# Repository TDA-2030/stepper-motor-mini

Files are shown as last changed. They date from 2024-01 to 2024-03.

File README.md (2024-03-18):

# Stepper Motor mini

A very simple and low-cost  stepper motor controller based on [dummy robot](https://gitee.com/switchpi/dummy)

## How to build

build on Windows

1. Download toolchain from https://github.com/xpack-dev-tools/arm-none-eabi-gcc-xpack/releases and unzip it.
2. run follow command to build
    ```shell
    mkdir build
    cmake -G "MinGW Makefiles" ..
    ```

## Feature

- Power: 12v~24v
- 2-layer board
- mini size
- Modbus support

## Preview

<center>
<figure>
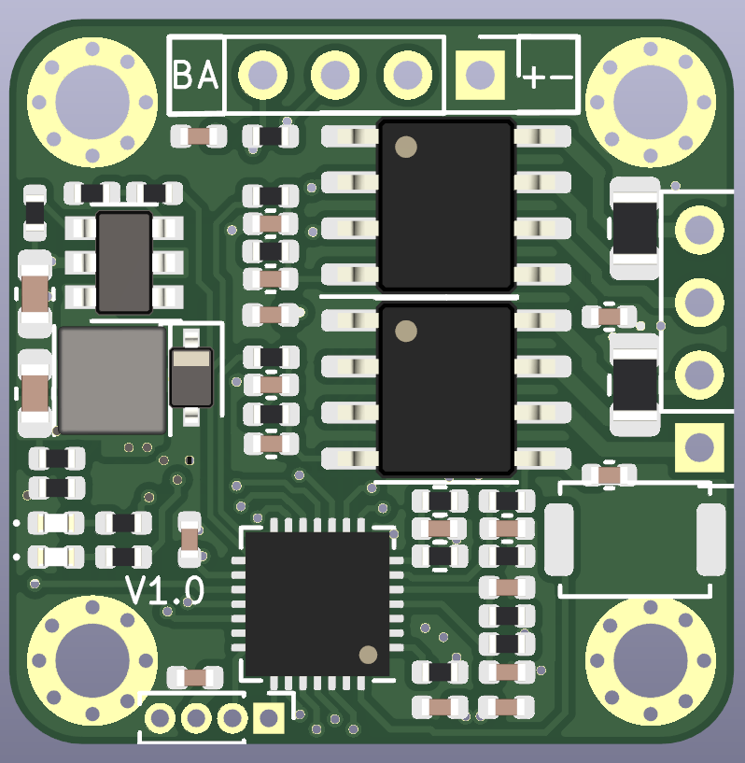
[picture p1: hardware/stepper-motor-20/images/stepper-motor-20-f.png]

·
·
·
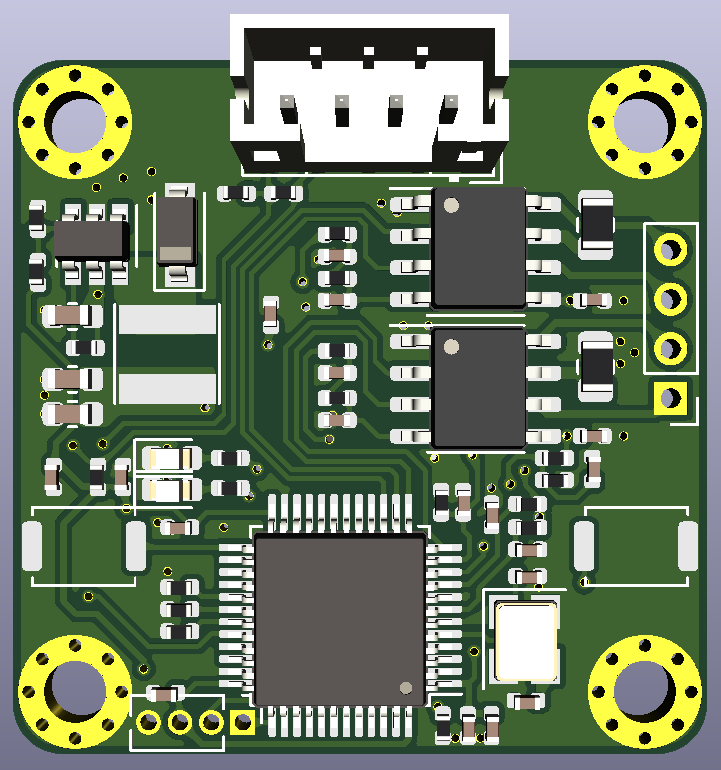
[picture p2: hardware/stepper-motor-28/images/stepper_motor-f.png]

</figure>
</center>

## Uasge

### Button Functions

| Action | Function |
| --- | --- |
| click | toggle to run or stop |
| long press | restore settings |

### calibration

push down the button then power on, the motor well start to calibration sensor.

### Modbus Register

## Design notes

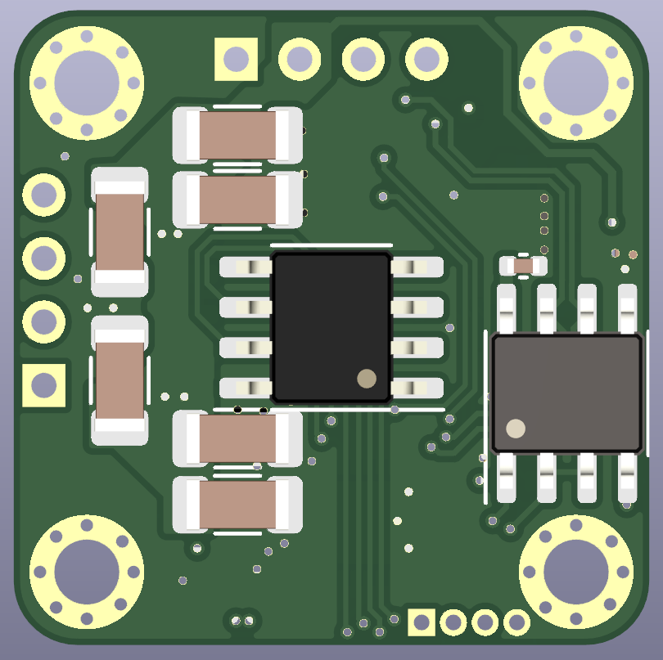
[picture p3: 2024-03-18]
hardware/stepper-motor-20/images/stepper-motor-20-b.png

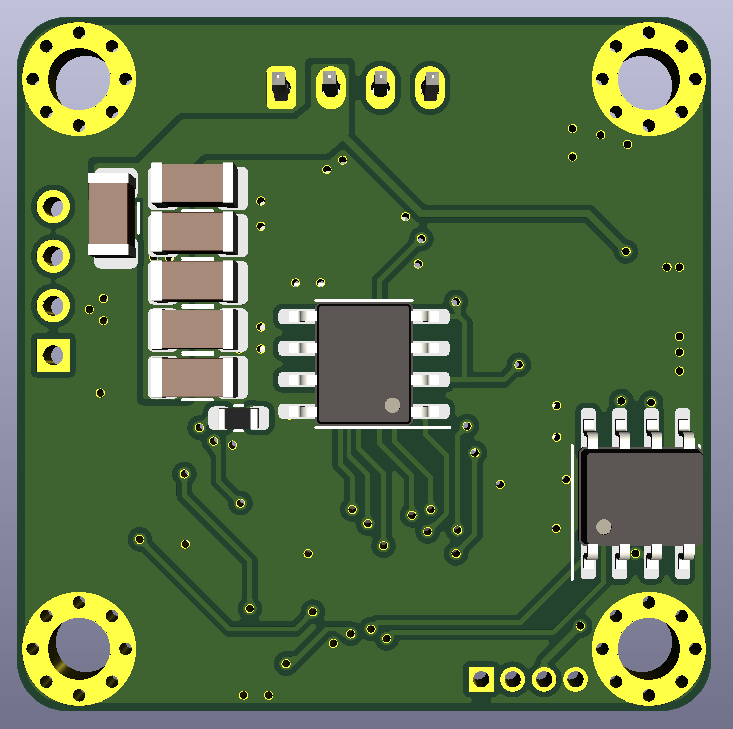
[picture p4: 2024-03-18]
hardware/stepper-motor-28/images/stepper_motor-b.png

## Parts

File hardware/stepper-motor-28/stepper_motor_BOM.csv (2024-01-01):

Comment | Description | Designator | Footprint | LibRef | Pins | Quantity | PartNumber | url
15p | desc | C1,C2, | C_0402_1005Metric | libref | 2 | 2
100n | desc | C3,C8,C11,C12,C15,C16,C19,C20,C28,C29, | C_0402_1005Metric | libref | 2 | 10
2.2u | desc | C4,C5,C6,C7,C9,C10,C24, | C_0402_1005Metric | libref | 2 | 7
10uf | desc | C25,C26,C27, | C_0603_1608Metric | libref | 2 | 3
GREEN | desc | D1, | LED_0603_1608Metric | libref | 2 | 1
RED | desc | D2, | LED_0603_1608Metric | libref | 2 | 1
B5819W SL | desc | D3, | D_SOD-123 | libref | 2 | 1
22uH | desc | L1, | L_Taiyo-Yuden_NR-40xx | libref | 2 | 1
1k | desc | R1,R2,R6,R7,R8,R9,R17, | R_0402_1005Metric | libref | 2 | 7
10k | desc | R3,R4,R16, | R_0402_1005Metric | libref | 2 | 3
0Ω | desc | R5,R21,R22,R23, | R_0402_1005Metric | libref | 2 | 4
0.1Ω | desc | R10,R11, | R_0805_2012Metric | libref | 2 | 2
3.3k | desc | R12, | R_0402_1005Metric | libref | 2 | 1
200k | desc | R13, | R_0402_1005Metric | libref | 2 | 1
33k | desc | R14, | R_0402_1005Metric | libref | 2 | 1
100k | desc | R15, | R_0402_1005Metric | libref | 2 | 1
120R | desc | R18, | R_0402_1005Metric | libref | 2 | 1
360R | desc | R19,R20, | R_0402_1005Metric | libref | 2 | 2
STM32F103CBTx | desc | U2, | LQFP-48_7x7mm_P0.5mm | libref | 48 | 1
TB67H450FNG | desc | U3,U4, | SOIC-8-1EP_3.9x4.9mm_P1.27mm_EP2.41x3.3mm | libref | 13 | 2
TX4137 | desc | U5, | SOT-23-6 | libref | 6 | 1
8MHz | desc | Y1, | Crystal_SMD_3225-4Pin_3.2x2.5mm | libref | 4 | 1
SW_Push | desc | SW2,SW3, | SW_Push_SPST_NO_Alps_SKRK | libref | 2 | 2
22uF, 25V | desc | C13,C14,C17,C18,C21,C22, | C_1206_3216Metric | libref | 2 | 6
MT6816 | desc | U1, | SOIC-8_3.9x4.9mm_P1.27mm | libref | 8 | 1
SP3485EP | desc | U6, | SOIC-8_3.9x4.9mm_P1.27mm | libref | 8 | 1
NTC 10k | desc | NTC1, | R_0603_1608Metric | libref | 2 | 1
Through Hole Items
MountingHole_Pad | desc | H1,H2,H3,H4, | MountingHole_2.5mm_Pad_Via | libref | 9 | 4
CON | desc | J1, | JST_PH_B4B-PH-K_1x04_P2.00mm_Vertical | libref | 4 | 1
SWD | desc | J2, | PinHeader_1x04_P1.27mm_Vertical | libref | 4 | 1
MOTOR | desc | J3, | PinHeader_1x04_P2.00mm_Vertical | libref | 4 | 1

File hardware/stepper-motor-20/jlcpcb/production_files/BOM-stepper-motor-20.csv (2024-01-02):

Comment | Designator | Footprint | LCSC
100n | C3 | C_0402_1005Metric
2.2u | C4 | C_0402_1005Metric
2.2u | C5 | C_0402_1005Metric
2.2u | C6 | C_0402_1005Metric
2.2u | C7 | C_0402_1005Metric
100n | C8 | C_0402_1005Metric
2.2u | C9 | C_0402_1005Metric
2.2u | C10 | C_0402_1005Metric
100n | C12 | C_0402_1005Metric
100n | C16 | C_0402_1005Metric
100n | C19 | C_0402_1005Metric
100n | C20 | C_0402_1005Metric
10uf | C24 | C_0603_1608Metric
100n | C26 | C_0402_1005Metric
GREEN | D1 | LED_0402_1005Metric
RED | D2 | LED_0402_1005Metric
1N5819 | D3 | D_SOD-323
MountingHole_Pad | H1 | MountingHole_2.0mm_Pad_Via
MountingHole_Pad | H2 | MountingHole_2.0mm_Pad_Via
MountingHole_Pad | H3 | MountingHole_2.0mm_Pad_Via
SWD | J2 | PinHeader_1x04_P1.00mm_Vertical
MOTOR | J3 | PinHeader_1x04_P2.00mm_Vertical
22uH | L1 | L_Taiyo-Yuden_MD-3030
1k | R2 | R_0402_1005Metric
10k | R3 | R_0402_1005Metric
10k | R4 | R_0402_1005Metric
0Ω | R5 | R_0402_1005Metric
1k | R7 | R_0402_1005Metric
1k | R9 | R_0402_1005Metric
0.1Ω | R10 | R_0805_2012Metric
0.1Ω | R11 | R_0805_2012Metric
200k | R12 | R_0402_1005Metric
33k | R13 | R_0402_1005Metric
100k | R14 | R_0402_1005Metric
10k | R15 | R_0402_1005Metric
120R | R18 | R_0402_1005Metric
4.7k | R19 | R_0402_1005Metric
GD32F150G8U6TR | U2 | QFN-28-1EP_4x4mm_P0.4mm_EP2.6x2.6mm
TB67H450FNG | U3 | SOIC-8-1EP_3.9x4.9mm_P1.27mm_EP2.41x3.3mm
TB67H450FNG | U4 | SOIC-8-1EP_3.9x4.9mm_P1.27mm_EP2.41x3.3mm
TX4137 | U5 | SOT-23-6
MountingHole_Pad | H4 | MountingHole_2.0mm_Pad_Via
1k | R16 | R_0402_1005Metric
3.3k | R17 | R_0402_1005Metric
1k | R1 | R_0402_1005Metric
4.7k | R20 | R_0402_1005Metric
1k | R6 | R_0402_1005Metric
CON | J1 | PinHeader_1x04_P2.00mm_Vertical
1k | R8 | R_0402_1005Metric
100n | C15 | C_0402_1005Metric
100n | C11 | C_0402_1005Metric
SW_Push | SW1 | SW_Push_SPST_NO_Alps_SKRK
2.2u | C27 | C_0402_1005Metric
NTC 10k | NTC1 | R_0402_1005Metric
10uf | C23 | C_0603_1608Metric
22uF, 25V | C13 | C_1206_3216Metric
22uF, 25V | C14 | C_1206_3216Metric
22uF, 25V | C17 | C_1206_3216Metric
22uF, 25V | C18 | C_1206_3216Metric
22uF, 25V | C21 | C_1206_3216Metric
22uF, 25V | C22 | C_1206_3216Metric
MT6816 | U1 | SOP-8_3.76x4.96mm_P1.27mm
SP3485EP | U6 | SOIC-8_3.9x4.9mm_P1.27mm
100n | C28 | C_0402_1005Metric

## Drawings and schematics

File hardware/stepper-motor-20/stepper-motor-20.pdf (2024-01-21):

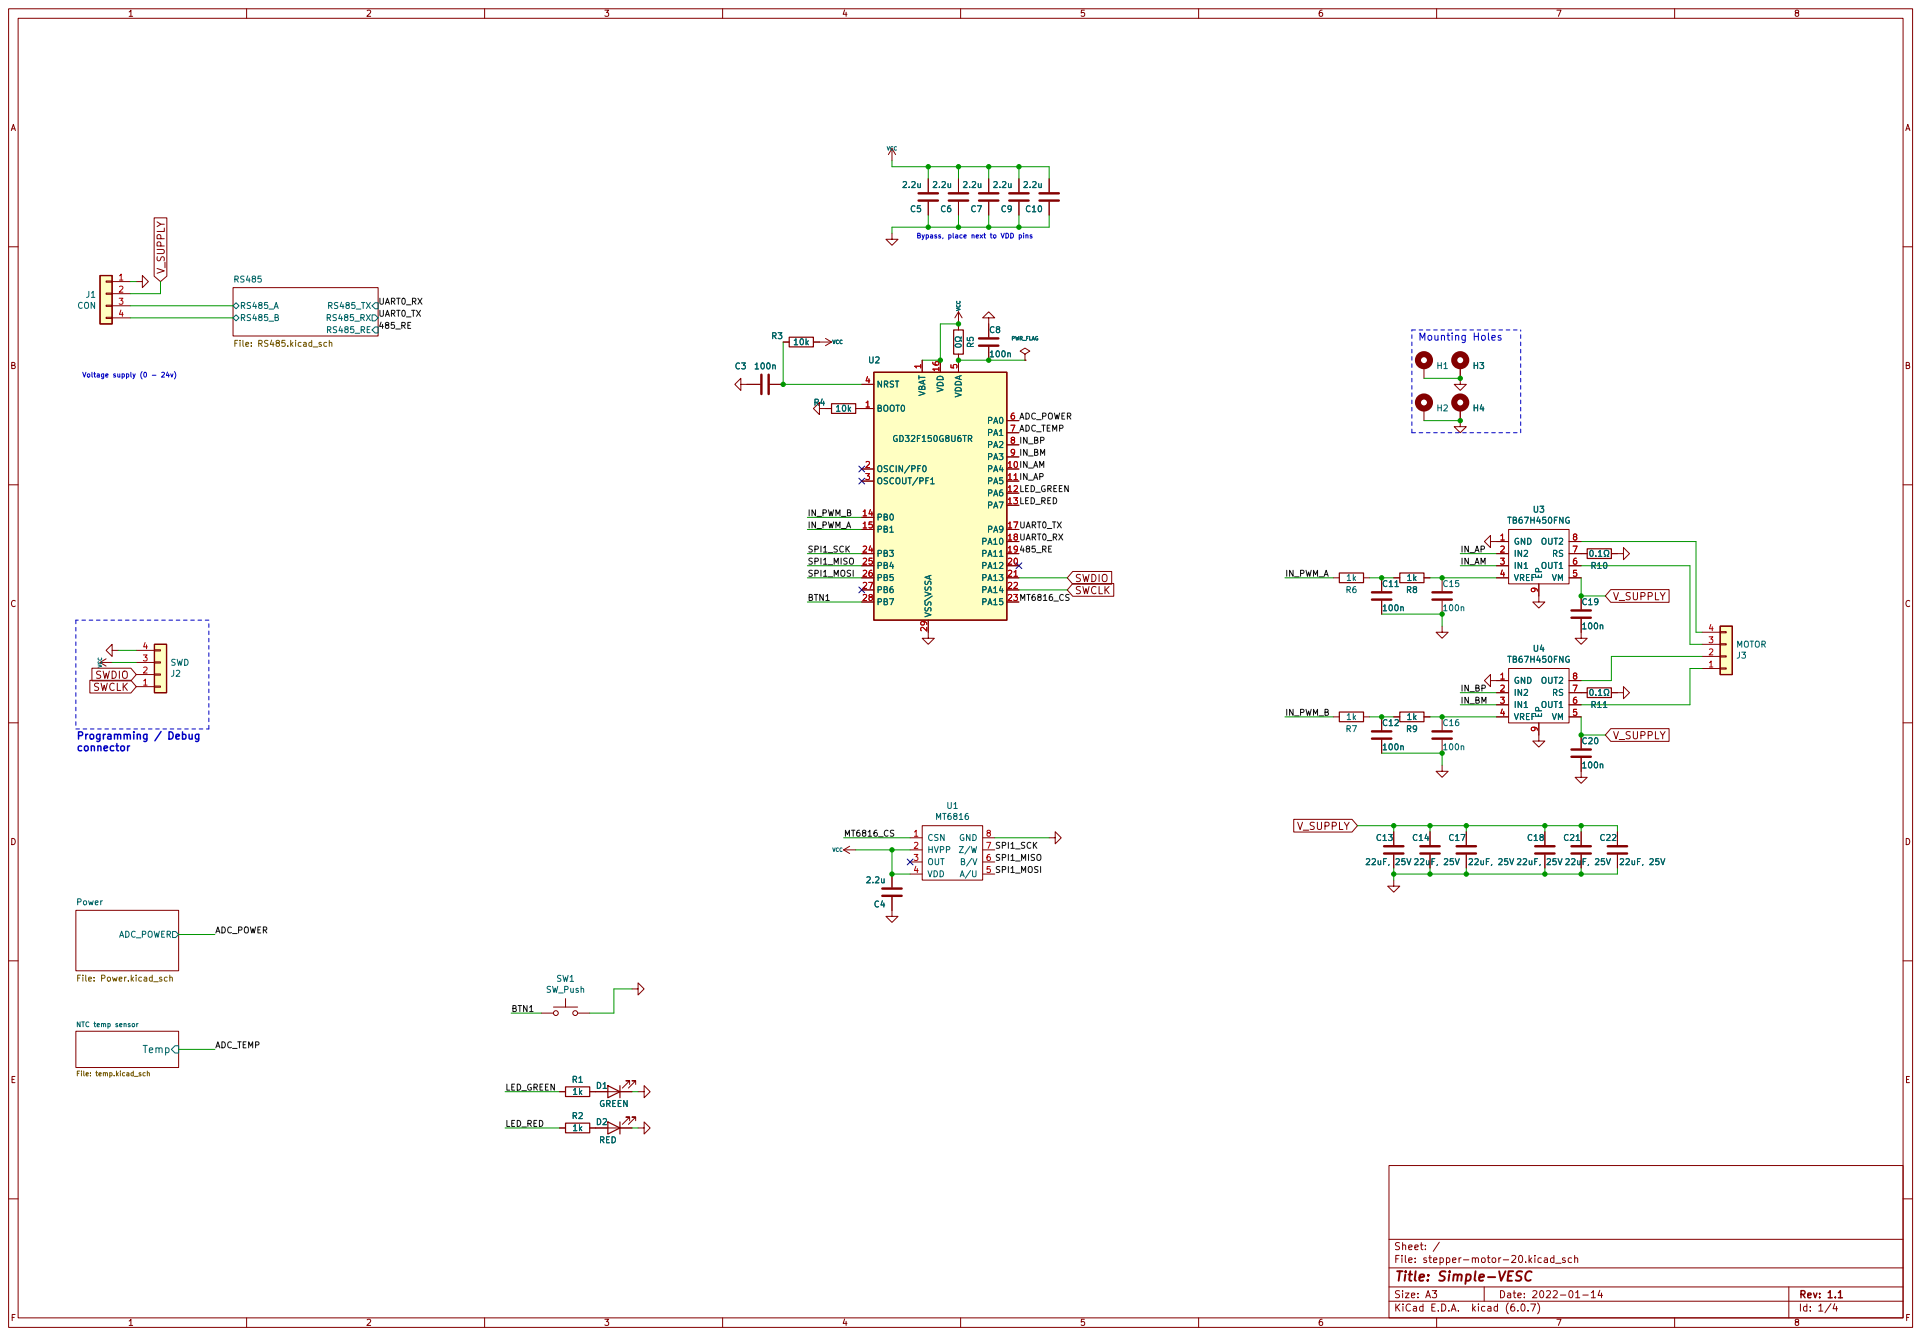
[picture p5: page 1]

V_SUPPLY
Voltage supply (0 - 24v) Programming / Debug

Bypass, place next to VDD pins

1 PA4 10 PA5 11 PA6 12 PA7 13 PB0 14 PB1 15 VDD 16 PA9 17 PA10 18 PA11 19 OSCIN/PF0 2 PA12 20 PA13 21 PA14 22 PA15 23 PB3 24 PB4 25 PB5 26 PB6 27 PB7 28 VSS\VSSA 29 OSCOUT/PF1 3 NRST 4 VDDA

NTC temp sensor File: temp.kicad_sch ADC_POWER

File: stepper-motor-20.kicad_sch Sheet: / Temp

Id: 1/4 Title: Simple-VESC

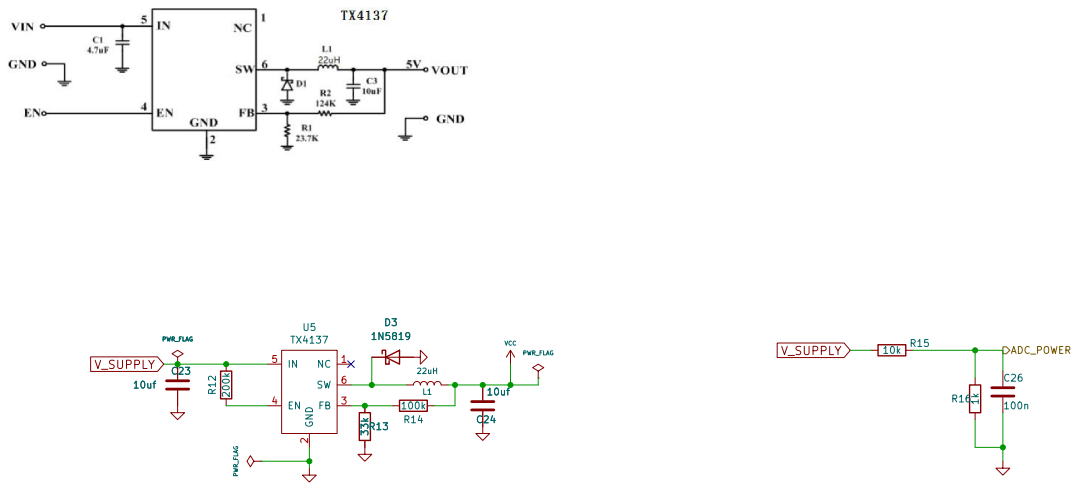
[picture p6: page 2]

File: Power.kicad_sch Sheet: /Power/ R13 33k

Id: 2/4 Title: Simple-VESC

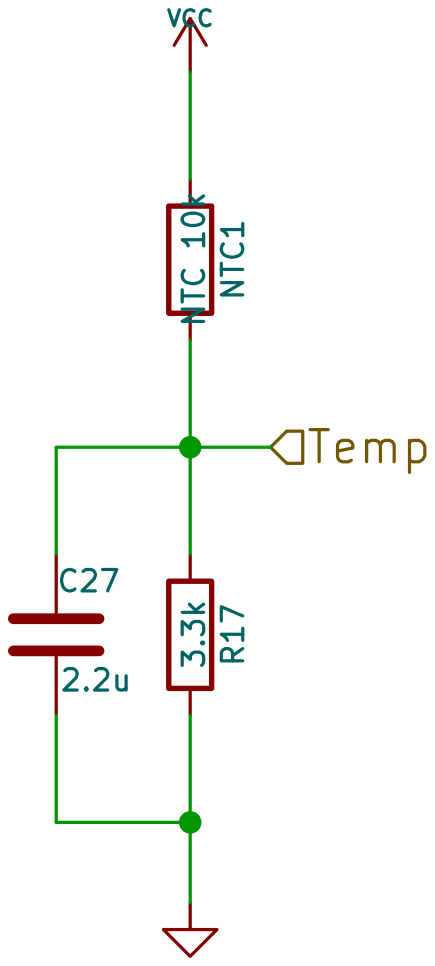
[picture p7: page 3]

Sheet: /NTC temp sensor/ 3.3k R17 C27

File: temp.kicad_sch
Id: 3/4 Title: Simple-VESC

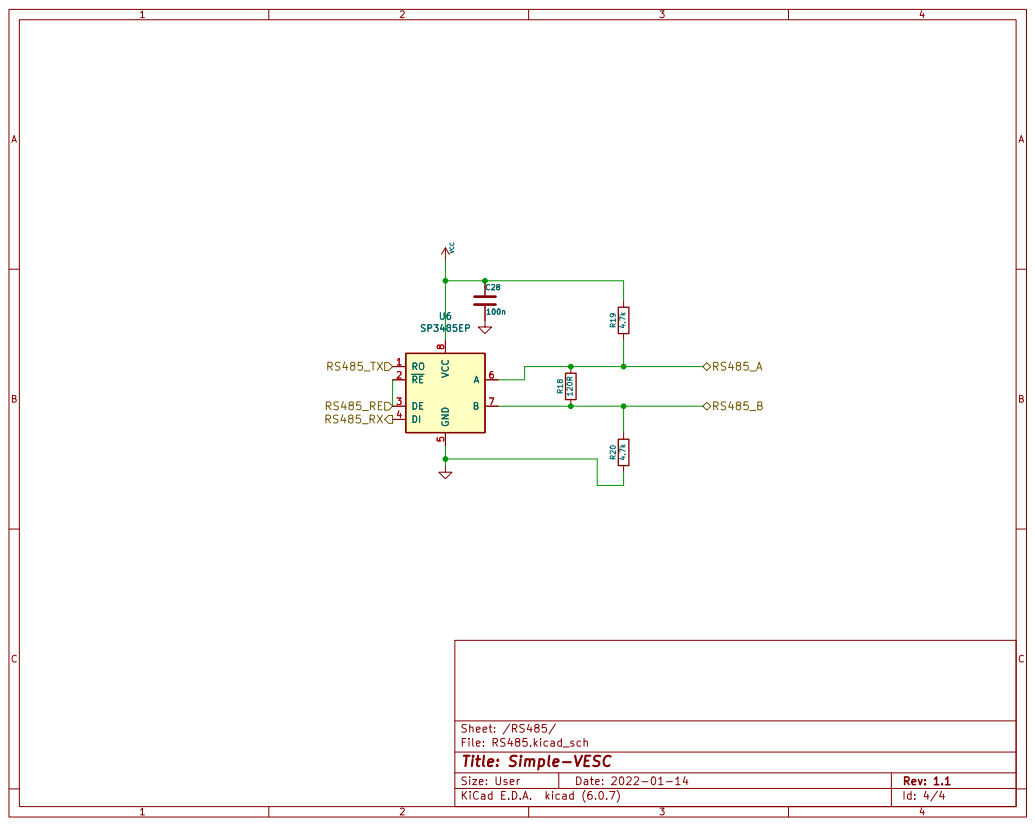
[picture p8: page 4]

Id: 4/4 Title: Simple-VESC

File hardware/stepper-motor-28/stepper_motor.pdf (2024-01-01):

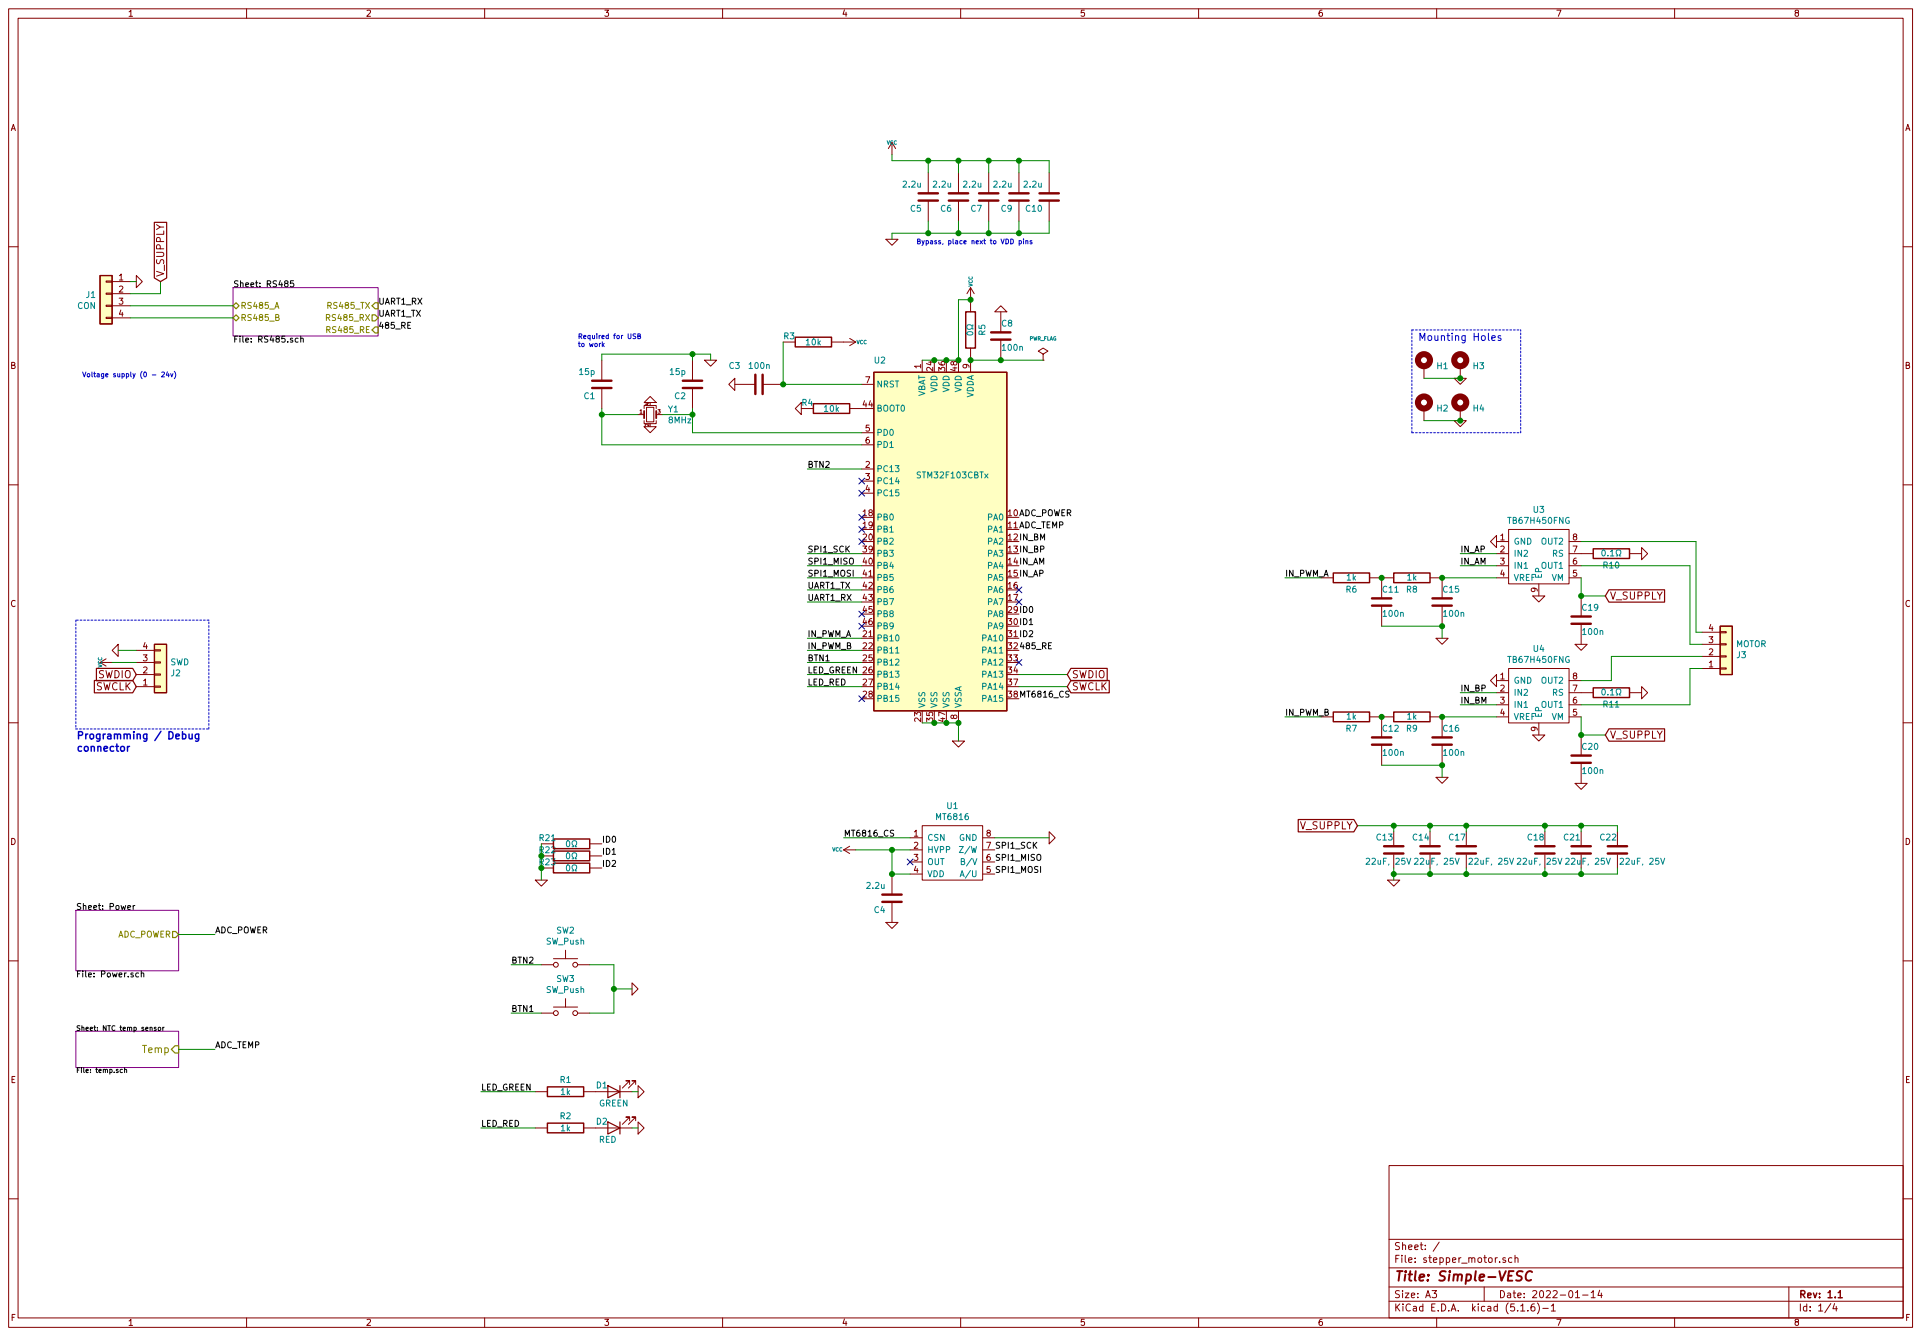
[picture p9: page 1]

Bypass, place next to VDD pins Required for USB

to work Programming / Debug

1 VDD 24 VDD 36 VDD 48 VDDA

9 VSS 23 VSS 35 VSS 47 VSSA

Sheet: Power File: Power.sch ADC_POWER

Id: 1/4 Title: Simple-VESC

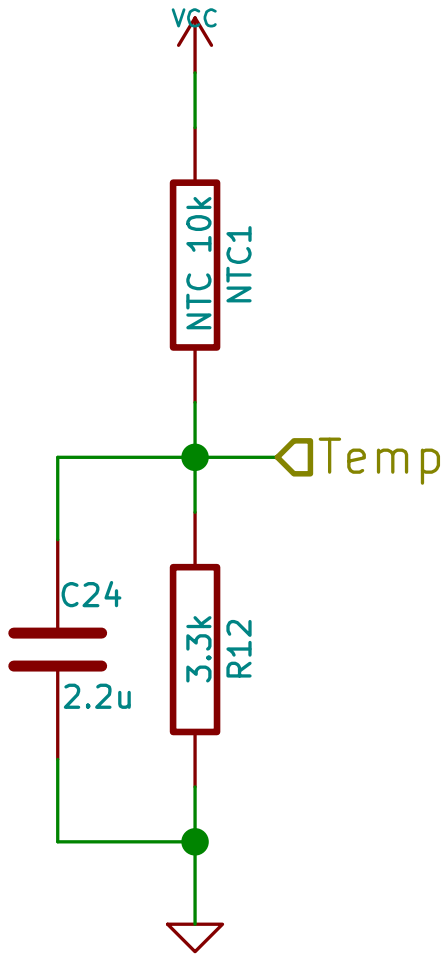
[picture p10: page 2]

Sheet: /NTC temp sensor/ 3.3k R12 C24

File: temp.sch
Id: 2/4 Title: Simple-VESC

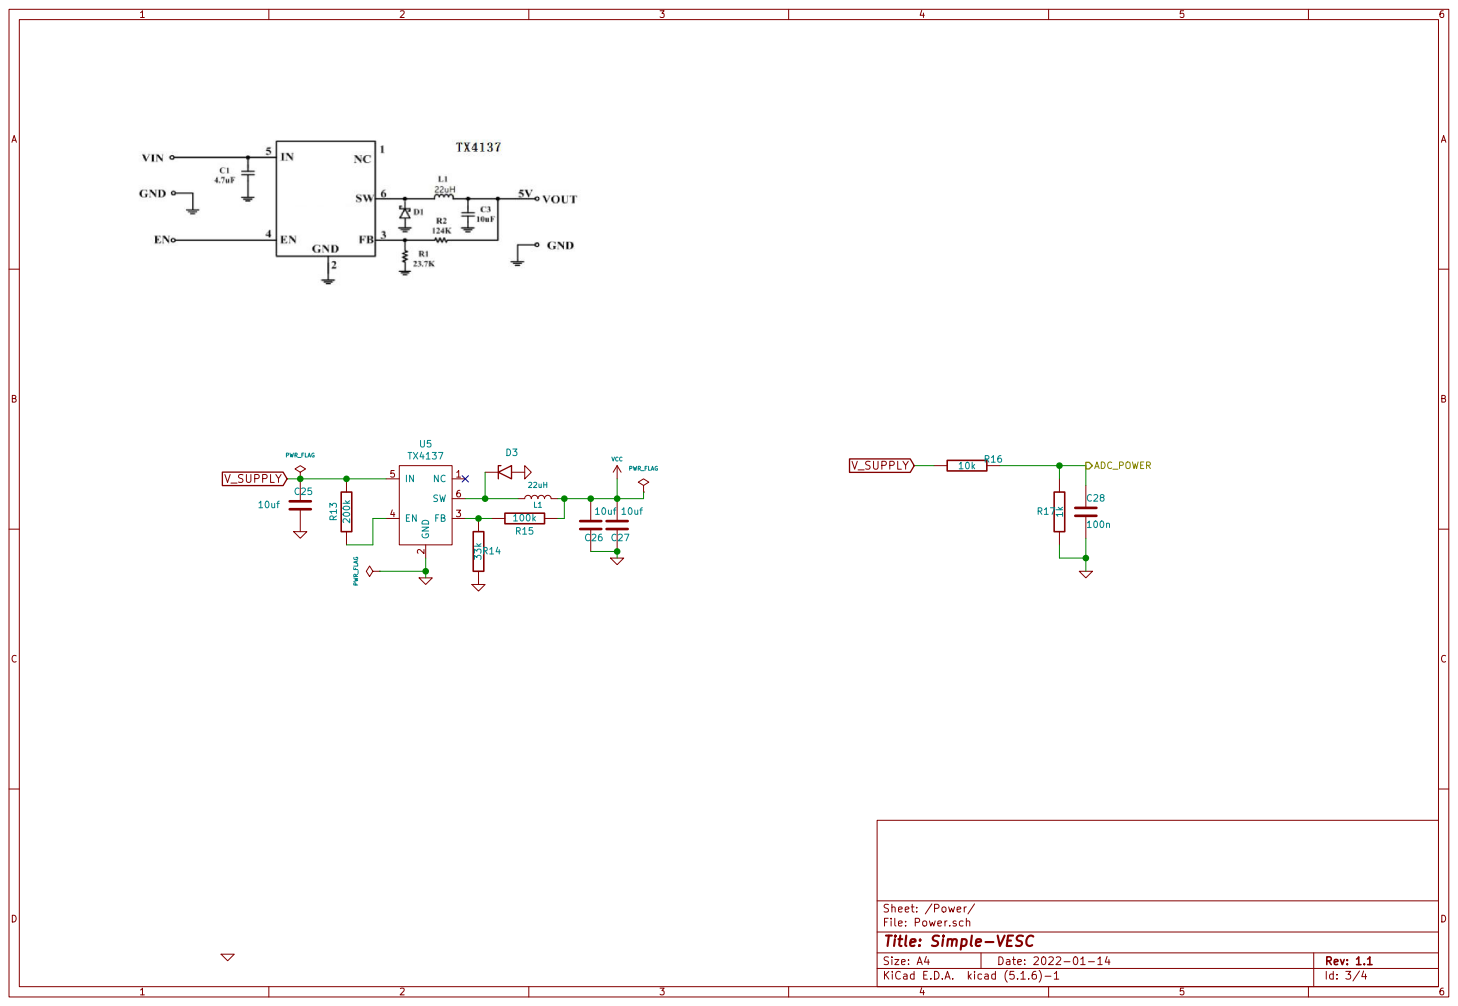
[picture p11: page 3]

File: Power.sch Sheet: /Power/ C26

Id: 3/4 Title: Simple-VESC

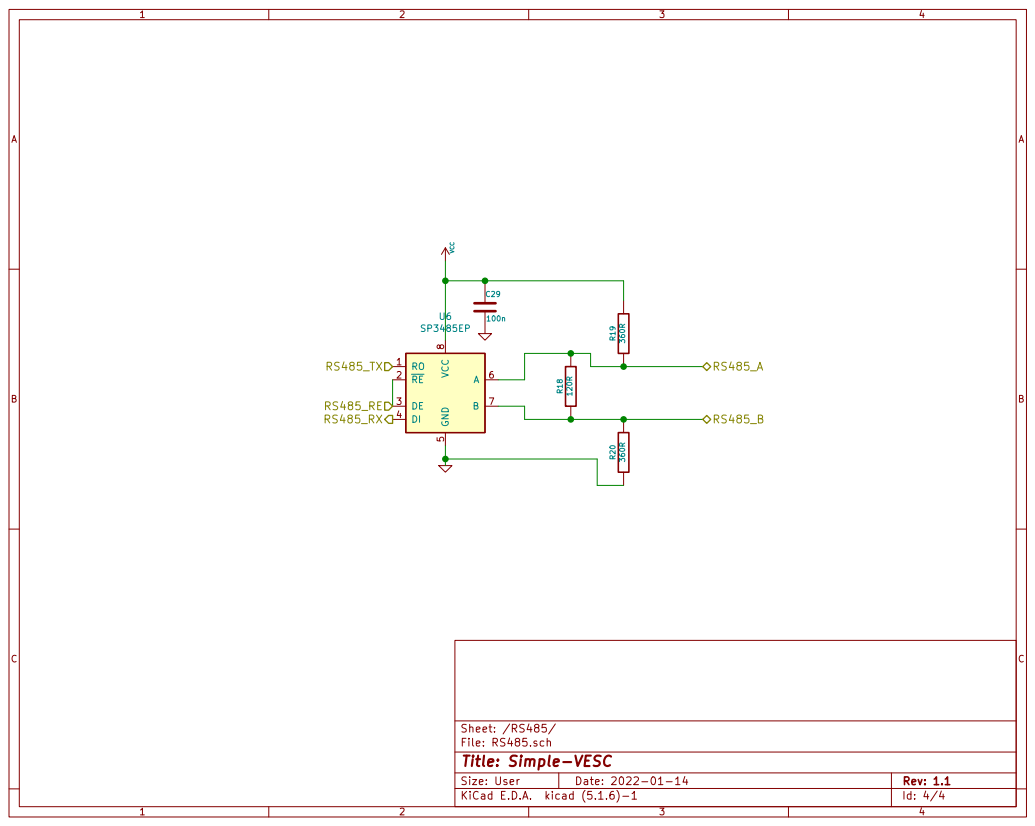
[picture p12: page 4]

Id: 4/4 Title: Simple-VESC

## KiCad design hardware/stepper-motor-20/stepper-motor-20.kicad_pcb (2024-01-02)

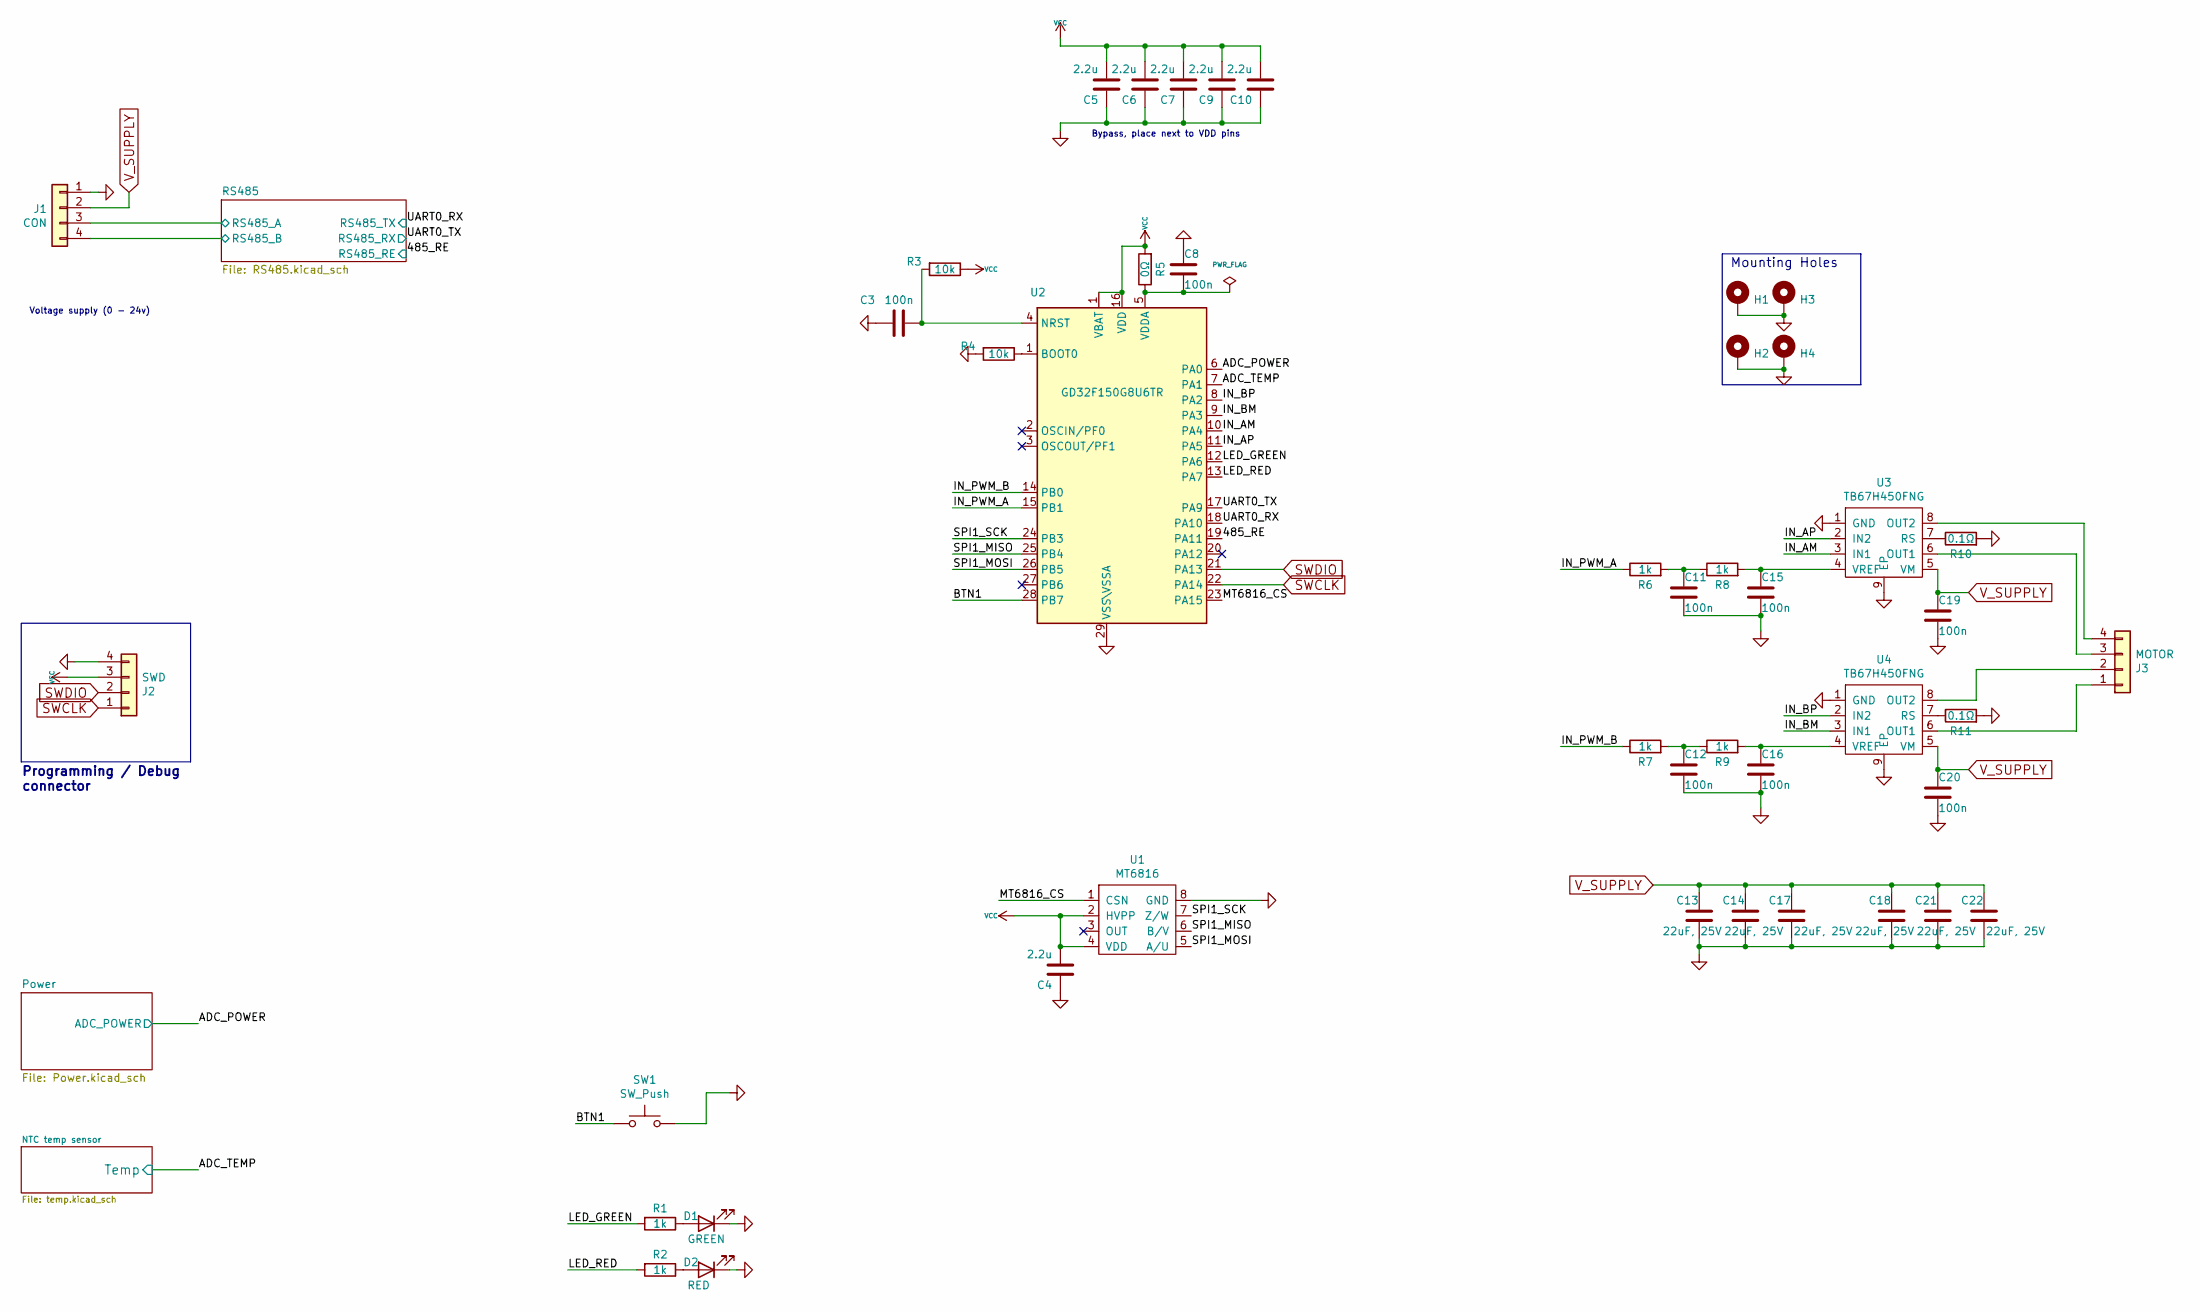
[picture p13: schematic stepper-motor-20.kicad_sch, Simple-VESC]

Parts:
C3, C8, C11, C12, C15, C16, C19, C20: 100n; C_0402_1005Metric
C4, C5, C6, C7, C9, C10: 2.2u; C_0402_1005Metric
C13, C14, C17, C18, C21, C22: 22uF, 25V; C_1206_3216Metric
D1: GREEN; LED_0402_1005Metric
D2: RED; LED_0402_1005Metric
H1, H2, H3, H4: MountingHole_Pad; MountingHole_2.0mm_Pad_Via
J1: CON; PinHeader_1x04_P2.00mm_Vertical
J2: SWD; PinHeader_1x04_P1.00mm_Vertical
J3: MOTOR; PinHeader_1x04_P2.00mm_Vertical
R1, R2, R6, R7, R8, R9: 1k; R_0402_1005Metric
R3, R4: 10k; R_0402_1005Metric
R5: 0Ω; R_0402_1005Metric
R10, R11: 0.1Ω; R_0805_2012Metric
SW1: SW_Push; SW_Push_SPST_NO_Alps_SKRK
U1: MT6816; SOP-8_3.76x4.96mm_P1.27mm
U2: GD32F150G8U6TR; QFN-28-1EP_4x4mm_P0.4mm_EP2.6x2.6mm
U3, U4: TB67H450FNG; SOIC-8-1EP_3.9x4.9mm_P1.27mm_EP2.41x3.3mm

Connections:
/485_RE: U2.19 (PA11); also elsewhere on the board
/ADC_POWER: U2.6 (PA0); also elsewhere on the board
/ADC_TEMP: U2.7 (PA1); also elsewhere on the board
/BTN1: SW1.1, U2.28 (PB7)
/IN_AM: U2.10 (PA4), U3.3 (IN1)
/IN_AP: U2.11 (PA5), U3.2 (IN2)
/IN_BM: U2.9 (PA3), U4.3 (IN1)
/IN_BP: U2.8 (PA2), U4.2 (IN2)
/IN_PWM_A: R6.1, U2.15 (PB1)
/IN_PWM_B: R7.1, U2.14 (PB0)
/LED_GREEN: R1.2, U2.12 (PA6)
/LED_RED: R2.2, U2.13 (PA7)
/MT6816_CS: U1.1 (CSN), U2.23 (PA15)
/RS485/RS485_A: J1.3; also elsewhere on the board
/RS485/RS485_B: J1.4; also elsewhere on the board
/SPI1_MISO: U1.6 (B/V), U2.25 (PB4)
/SPI1_MOSI: U1.5 (A/U), U2.26 (PB5)
/SPI1_SCK: U1.7 (Z/W), U2.24 (PB3)
/UART0_RX: U2.18 (PA10); also elsewhere on the board
/UART0_TX: U2.17 (PA9); also elsewhere on the board
unnamed: C3.2, R3.2, U2.4 (NRST)
unnamed: C8.1, R5.1, U2.5 (VDDA)
unnamed: C11.2, R6.2, R8.1
unnamed: C12.2, R7.2, R9.1
unnamed: C15.2, R8.2, U3.4 (VREF)
unnamed: C16.2, R9.2, U4.4 (VREF)
unnamed: D1.2 (A), R1.1
unnamed: D2.2 (A), R2.1
unnamed: J3.1, U4.6 (OUT1)
unnamed: J3.2, U4.8 (OUT2)
unnamed: J3.3, U3.6 (OUT1)
unnamed: J3.4, U3.8 (OUT2)
unnamed: R10.1, U3.7 (RS)
unnamed: R11.1, U4.7 (RS)
SWCLK: J2.1, U2.22 (PA14)
SWDIO: J2.2, U2.21 (PA13)
V_SUPPLY: C13.2, C14.2, C17.2, C18.2, C19.2, C20.2, C21.2, C22.2, J1.2, U3.5 (VM), U4.5 (VM); also elsewhere on the board

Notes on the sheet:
Programming / Debug connector
Voltage supply (0 - 24v)
Mounting Holes
Bypass, place next to VDD pins

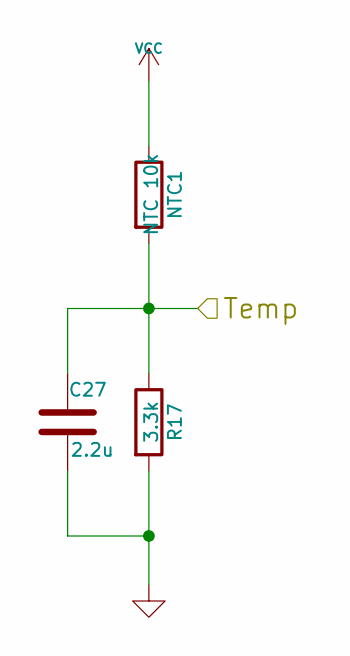
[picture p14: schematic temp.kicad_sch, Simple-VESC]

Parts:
C27: 2.2u; C_0402_1005Metric
NTC1: NTC 10k; R_0402_1005Metric
R17: 3.3k; R_0402_1005Metric

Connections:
/ADC_TEMP: C27.1, NTC1.2, R17.1; also elsewhere on the board

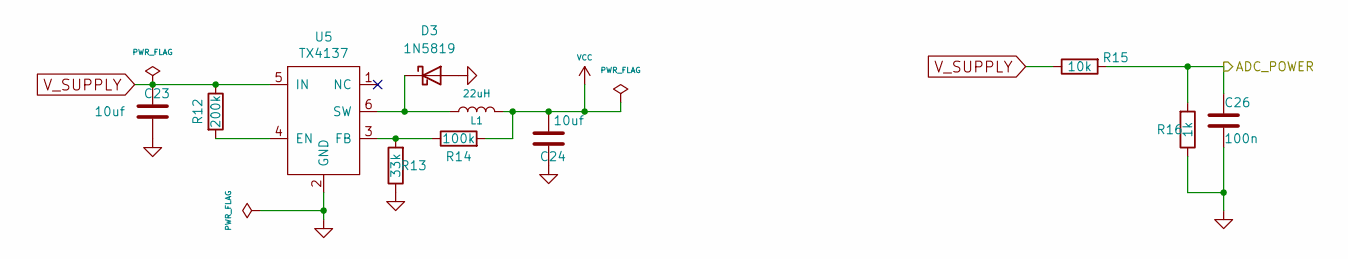
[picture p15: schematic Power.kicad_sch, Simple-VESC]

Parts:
C23, C24: 10uf; C_0603_1608Metric
C26: 100n; C_0402_1005Metric
D3: 1N5819; D_SOD-323
L1: 22uH; L_Taiyo-Yuden_MD-3030
R12: 200k; R_0402_1005Metric
R13: 33k; R_0402_1005Metric
R14: 100k; R_0402_1005Metric
R15: 10k; R_0402_1005Metric
R16: 1k; R_0402_1005Metric
U5: TX4137; SOT-23-6

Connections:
/ADC_POWER: C26.2, R15.2, R16.2; also elsewhere on the board
unnamed: D3.1 (K), L1.1, U5.6 (SW)
unnamed: R12.2, U5.4 (EN)
unnamed: R13.2, R14.1, U5.3 (FB)
V_SUPPLY: C23.2, R12.1, R15.1, U5.5 (IN); also elsewhere on the board

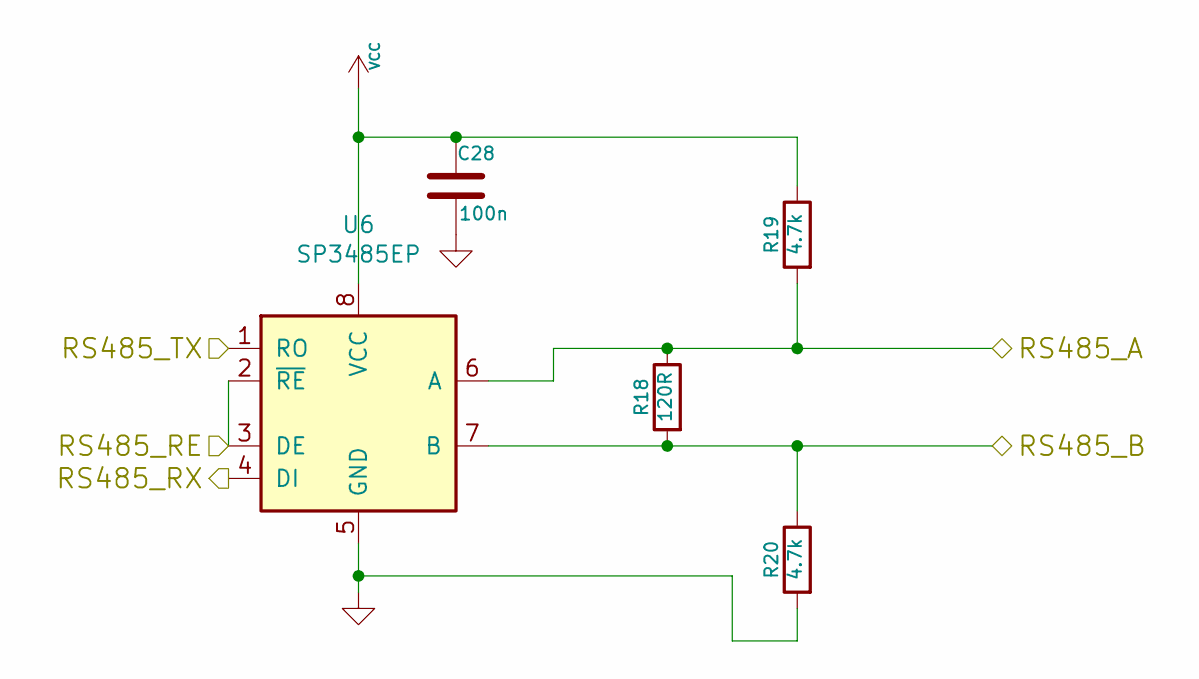
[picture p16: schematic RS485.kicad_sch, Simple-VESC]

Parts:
C28: 100n; C_0402_1005Metric
R18: 120R; R_0402_1005Metric
R19, R20: 4.7k; R_0402_1005Metric
U6: SP3485EP; SOIC-8_3.9x4.9mm_P1.27mm

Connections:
/485_RE: U6.2 (~RE), U6.3 (DE); also elsewhere on the board
/RS485/RS485_A: R18.1, R19.2, U6.6 (A); also elsewhere on the board
/RS485/RS485_B: R18.2, R20.1, U6.7 (B); also elsewhere on the board
/UART0_RX: U6.1 (RO); also elsewhere on the board
/UART0_TX: U6.4 (DI); also elsewhere on the board

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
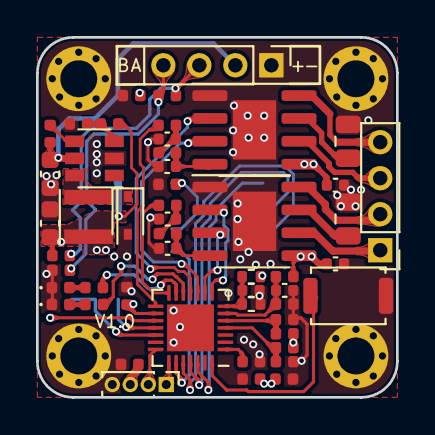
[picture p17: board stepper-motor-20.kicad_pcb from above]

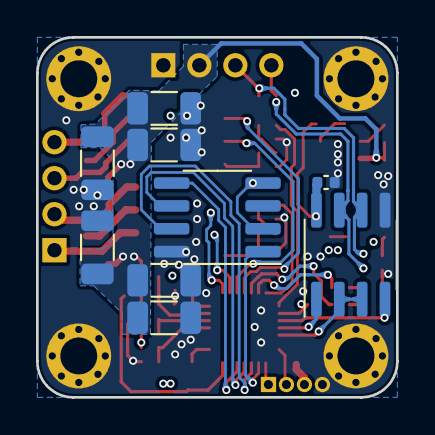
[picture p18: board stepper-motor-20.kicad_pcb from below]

Board: 4 copper layers, 20.0 x 20.0 mm, 64 parts (9 on the bottom side), 43 nets.

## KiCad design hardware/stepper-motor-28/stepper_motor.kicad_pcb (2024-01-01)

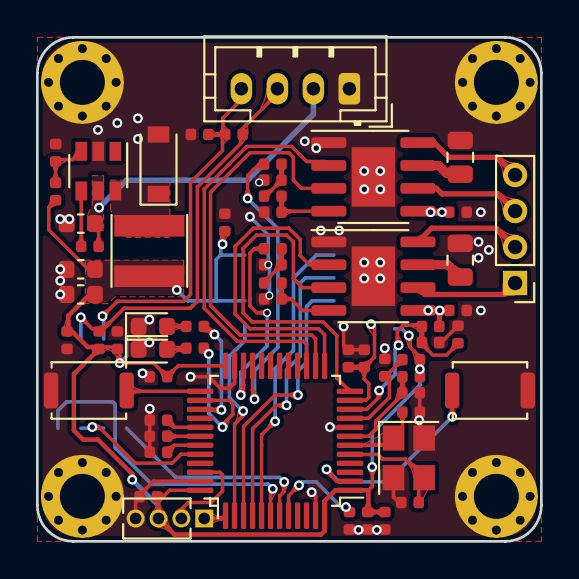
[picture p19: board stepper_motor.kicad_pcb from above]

Board: 2 copper layers, 28.0 x 28.0 mm, 72 parts (0 on the bottom side), 49 nets.

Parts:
C1, C2: 15p; C_0402_1005Metric
C3, C8, C11, C12, C15, C16, C19, C20, C28, C29: 100n; C_0402_1005Metric
C4, C5, C6, C7, C9, C10, C24: 2.2u; C_0402_1005Metric
C13, C14, C17, C18, C21, C22: 22uF, 25V; C_1206_3216Metric
C25, C26, C27: 10uf; C_0603_1608Metric
D1: GREEN; LED_0603_1608Metric
D2: RED; LED_0603_1608Metric
D3: B5819W SL; D_SOD-123
H1, H2, H3, H4: MountingHole_Pad; MountingHole_2.5mm_Pad_Via
J1: CON; JST_PH_B4B-PH-K_1x04_P2.00mm_Vertical
J2: SWD; PinHeader_1x04_P1.27mm_Vertical
J3: MOTOR; PinHeader_1x04_P2.00mm_Vertical
L1: 22uH; L_Taiyo-Yuden_NR-40xx
NTC1: NTC 10k; R_0603_1608Metric
R1, R2, R6, R7, R8, R9, R17: 1k; R_0402_1005Metric
R3, R4, R16: 10k; R_0402_1005Metric
R5, R21, R22, R23: 0Ω; R_0402_1005Metric
R10, R11: 0.1Ω; R_0805_2012Metric
R12: 3.3k; R_0402_1005Metric
R13: 200k; R_0402_1005Metric
R14: 33k; R_0402_1005Metric
R15: 100k; R_0402_1005Metric
R18: 120R; R_0402_1005Metric
R19, R20: 360R; R_0402_1005Metric
SW2, SW3: SW_Push; SW_Push_SPST_NO_Alps_SKRK
U1: MT6816; SOIC-8_3.9x4.9mm_P1.27mm
U2: STM32F103CBTx; LQFP-48_7x7mm_P0.5mm
U3, U4: TB67H450FNG; SOIC-8-1EP_3.9x4.9mm_P1.27mm_EP2.41x3.3mm
U5: TX4137; SOT-23-6
U6: SP3485EP; SOIC-8_3.9x4.9mm_P1.27mm
Y1: 8MHz; Crystal_SMD_3225-4Pin_3.2x2.5mm

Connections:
/485_RE: U2.32, U6.2, U6.3
/ADC_POWER: C28.2, R16.2, R17.2, U2.10
/ADC_TEMP: C24.1, NTC1.2, R12.1, U2.11
/BTN1: SW3.1, U2.25
/BTN2: SW2.1, U2.2
/ID0: R21.1, U2.29
/ID1: R22.1, U2.30
/ID2: R23.1, U2.31
/IN_AM: U2.14, U3.3
/IN_AP: U2.15, U3.2
/IN_BM: U2.12, U4.3
/IN_BP: U2.13, U4.2
/IN_PWM_A: R6.1, U2.21
/IN_PWM_B: R7.1, U2.22
/LED_GREEN: R1.2, U2.26
/LED_RED: R2.2, U2.27
/MT6816_CS: U1.1, U2.38
/RS485/RS485_A: J1.3, R18.1, R19.2, U6.6
/RS485/RS485_B: J1.4, R18.2, R20.1, U6.7
/SPI1_MISO: U1.6, U2.40
/SPI1_MOSI: U1.5, U2.41
/SPI1_SCK: U1.7, U2.39
/UART1_RX: U2.43, U6.1
/UART1_TX: U2.42, U6.4
GND: C1.2, C2.2, C3.1, C4.1, C5.1, C6.1, C7.1, C8.2, C9.1, C10.1, C11.1, C12.1, C13.1, C14.1, C15.1, C16.1, C17.1, C18.1, C19.1, C20.1, C21.1, C22.1, C24.2, C25.1, C26.1, C27.1, C28.1, C29.2, D1.1, D2.1, D3.2, H1.1, H2.1, H3.1, H4.1, J1.1, J2.4, R4.2, R10.2, R11.2, R12.2, R14.1, R17.1, R20.2, R21.2, R22.2, R23.2, SW2.2, SW3.2, U1.8, U2.8, U2.23, U2.35, U2.47, U3.1, U3.9, U4.1, U4.9, U5.2, U6.5, Y1.2, Y1.4
unnamed: C1.1, U2.6, Y1.1
unnamed: C2.1, U2.5, Y1.3
unnamed: C3.2, R3.2, U2.7
unnamed: C8.1, R5.1, U2.9
unnamed: C11.2, R6.2, R8.1
unnamed: C12.2, R7.2, R9.1
unnamed: C15.2, R8.2, U3.4
unnamed: C16.2, R9.2, U4.4
unnamed: D1.2, R1.1
unnamed: D2.2, R2.1
unnamed: D3.1, L1.1, U5.6
unnamed: J3.1, U4.6
unnamed: J3.2, U4.8
unnamed: J3.3, U3.6
unnamed: J3.4, U3.8
unnamed: R4.1, U2.44
unnamed: R10.1, U3.7
unnamed: R11.1, U4.7
unnamed: R13.2, U5.4
unnamed: R14.2, R15.1, U5.3
SWCLK: J2.1, U2.37
SWDIO: J2.2, U2.34
VCC: C4.2, C5.2, C6.2, C7.2, C9.2, C10.2, C26.2, C27.2, C29.1, J2.3, L1.2, NTC1.1, R3.1, R5.2, R15.2, R19.1, U1.2, U1.4, U2.1, U2.24, U2.36, U2.48, U6.8
V_SUPPLY: C13.2, C14.2, C17.2, C18.2, C19.2, C20.2, C21.2, C22.2, C25.2, J1.2, R13.1, R16.1, U3.5, U4.5, U5.5

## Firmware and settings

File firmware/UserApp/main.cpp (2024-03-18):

#include "common_inc.h"
#include "Platform\Memory\eeprom_interface.h"
#include "configurations.h"
#include "Platform/utils.h"
#include "tim.h"
#include "usart.h"

#ifdef GD32F130_150
#include "systick.h"
#endif

/* Component Definitions -----------------------------------------------------*/
BoardConfig_t boardConfig;
Motor motor;
TB67H450 tb67H450;
MT6816 mt6816;
EncoderCalibrator encoderCalibrator(&motor);
Button button1(1, 2000), button2(2, 3000);
void OnButton1Event(Button::Event _event);
void OnButton2Event(Button::Event _event);
Led statusLed;


extern void modbus_init(uint8_t id);
extern void modbus_poll(void);


static void led_show_id(uint16_t id)
{
    for (size_t i = 0; i < 2; i++) {
        statusLed.Status(0, true);
        statusLed.Status(1, true);
        HAL_Delay(80);
        statusLed.Status(0, false);
        statusLed.Status(1, false);
        HAL_Delay(80);
    }
    HAL_Delay(200);

    id = id < 8 ? id : 8;
    for (size_t i = 0; i < id; i++) {
        statusLed.Status(1, true);
        HAL_Delay(150);
        statusLed.Status(1, false);
        HAL_Delay(150);
    }
    statusLed.Status(0, true);
    statusLed.Status(1, true);
    HAL_Delay(400);
    statusLed.Status(0, false);
    statusLed.Status(1, false);
}

/* Main Entry ----------------------------------------------------------------*/
extern "C" void Main()
{
    uint64_t serialNum = GetSerialNumber();
    uint16_t defaultNodeID = 0;

    /*---------- Apply EEPROM Settings ----------*/
    // Setting priority is EEPROM > Motor.h
    EEPROM eeprom;
    eeprom.get(0, boardConfig);
    if (boardConfig.configStatus != CONFIG_OK) { // use default settings
        boardConfig = BoardConfig_t{
            .configStatus = CONFIG_OK,
            .canNodeId = 1,
            .encoderHomeOffset = 0,
            .defaultMode = Motor::MODE_COMMAND_POSITION,
            .currentLimit = 1 * 1000,    // A
            .velocityLimit = 30 * motor.MOTOR_ONE_CIRCLE_SUBDIVIDE_STEPS, // r/s
            .velocityAcc = 100 * motor.MOTOR_ONE_CIRCLE_SUBDIVIDE_STEPS,   // r/s^2
            .calibrationCurrent = 2000,
#ifdef GD32F130_150
            .dce_kp = 250,
            .dce_kv = 80,
            .dce_ki = 100,
            .dce_kd = 500,
#elif defined(STM32F103xB)
            .dce_kp = 200,
            .dce_kv = 80,
            .dce_ki = 300,
            .dce_kd = 250,
#endif
            .motor_temperature = 0.0,
            .motor_temperature_threshold = 55,
            .motor_voltage_threshold_min = 10.5,
            .motor_voltage_threshold_max = 24.8,
            .enableMotorOnBoot = false,
            .enableStallProtect = false,
            .enableTempWatch = false,
            .reverse_direction = false,
        };
        eeprom.put(0, boardConfig);
    }
    led_show_id(boardConfig.canNodeId);
    // boardConfig.enableTempWatch=false;
    //depends on 3 bits switch now
    // boardConfig.canNodeId = defaultNodeID;
    motor.config.motionParams.encoderHomeOffset = boardConfig.encoderHomeOffset;
    motor.config.motionParams.ratedCurrent = boardConfig.currentLimit;
    motor.config.motionParams.ratedVelocity = boardConfig.velocityLimit;
    motor.config.motionParams.ratedVelocityAcc = boardConfig.velocityAcc;
    motor.motionPlanner.velocityTracker.SetVelocityAcc(boardConfig.velocityAcc);
    motor.motionPlanner.positionTracker.SetVelocityAcc(boardConfig.velocityAcc);
    motor.config.motionParams.caliCurrent = boardConfig.calibrationCurrent;
    motor.config.ctrlParams.dce.kp = boardConfig.dce_kp;
    motor.config.ctrlParams.dce.kv = boardConfig.dce_kv;
    motor.config.ctrlParams.dce.ki = boardConfig.dce_ki;
    motor.config.ctrlParams.dce.kd = boardConfig.dce_kd;
    motor.config.ctrlParams.stallProtectSwitch = boardConfig.enableStallProtect;


//    printf("encoderHomeOffset[%d] ratedCurrent[%d] ratedVelocity[%d] ratedVelocityAcc[%d]\r\n" , boardConfig.encoderHomeOffset, boardConfig.currentLimit, boardConfig.velocityLimit, boardConfig.velocityAcc);
//    printf("velocityTracker[%d] positionTracker[%d] caliCurrent[%d] \r\n" , boardConfig.velocityAcc, boardConfig.velocityAcc);
//    printf("kp[%d] kv[%d] ki[%d] kd[%d]\r\n" , boardConfig.dce_kp, boardConfig.dce_kv, boardConfig.dce_ki, boardConfig.dce_kd);


    /*---------------- Init Motor ----------------*/
    motor.AttachDriver(&tb67H450);
    motor.AttachEncoder(&mt6816);
    motor.controller->Init();
    motor.driver->Init();
    motor.encoder->Init();


    /*------------- Init peripherals -------------*/
    button1.SetOnEventListener(OnButton1Event);
    button2.SetOnEventListener(OnButton2Event);


    /*------- Start Close-Loop Control Tick ------*/
    HAL_Delay(100);
#ifdef GD32F130_150
    timer1_start();  // 100Hz
    timer13_start();  // 20kHz
#elif defined(STM32F103xB)
    HAL_TIM_Base_Start_IT(&htim1);  // 100Hz
    HAL_TIM_Base_Start_IT(&htim4);  // 20kHz
#endif

    if (button1.IsPressed()) {
        encoderCalibrator.isTriggered = true;
    }
//    printf("start motor %d\r\n", defaultNodeID);

    modbus_init(boardConfig.canNodeId);

    for (;;) {
//        if ( encoderCalibrator.FlashRun() == 0)
        encoderCalibrator.TickMainLoop();

        if (boardConfig.configStatus == CONFIG_COMMIT) {
            boardConfig.configStatus = CONFIG_OK;
            eeprom.put(0, boardConfig);
        } else if (boardConfig.configStatus == CONFIG_RESTORE) {
            eeprom.put(0, boardConfig);
            NVIC_SystemReset();
        }
        modbus_poll();
    }
}


/* Event Callbacks -----------------------------------------------------------*/
//let's add a global count in here for quick test
uint32_t count;
extern "C" void Tim1Callback100Hz()
{

    button1.Tick(10);
    button2.Tick(10);
    statusLed.Tick(10, motor.controller->state);
    //1s period to collect a temperature data
    count ++;
    if (0 == (count % 2)) {
        if (boardConfig.motor_voltage < boardConfig.motor_voltage_threshold_min) {
            motor.controller->requestMode = Motor::MODE_STOP;
            motor.controller->state = Motor::STATE_UNDERVOLTAGE;
        }
        if (boardConfig.motor_voltage > boardConfig.motor_voltage_threshold_max) {
            motor.controller->requestMode = Motor::MODE_STOP;
            motor.controller->state = Motor::STATE_OVERVOLTAGE;
        }
    }
    if ( count >= 100) {
        boardConfig.motor_temperature = AdcGetChipTemperature();
        boardConfig.motor_voltage = AdcGetVoltage();
        if (boardConfig.motor_temperature > boardConfig.motor_temperature_threshold) {
            motor.controller->requestMode = Motor::MODE_STOP;
            motor.controller->state = Motor::STATE_OVERTEMP;
        }
        count = 0;
    }
    if (boardConfig.enableTempWatch) {

    }
}


extern "C" void Tim4Callback20kHz()
{


    if (encoderCalibrator.isTriggered) {
        encoderCalibrator.Tick20kHz();
    } else {
        motor.Tick20kHz();
    }
}


void OnButton1Event(Button::Event _event)
{
    switch (_event) {
    case ButtonBase::UP:
        break;
    case ButtonBase::DOWN:
        break;
    case ButtonBase::LONG_PRESS:
        boardConfig.configStatus = CONFIG_RESTORE;
        break;
    case ButtonBase::CLICK:
        // printf("KEY1\r\n");
        if (motor.controller->modeRunning != Motor::MODE_STOP) {
            boardConfig.defaultMode = motor.controller->modeRunning;
            motor.controller->requestMode = Motor::MODE_STOP;
        } else {
            motor.controller->requestMode = static_cast<Motor::Mode_t>(boardConfig.defaultMode);
        }
        break;
    }
}


void OnButton2Event(Button::Event _event)
{
    switch (_event) {
    case ButtonBase::UP:
        break;
    case ButtonBase::DOWN:
        break;
    case ButtonBase::LONG_PRESS:
        switch (motor.controller->modeRunning) {
        case Motor::MODE_COMMAND_CURRENT:
        case Motor::MODE_PWM_CURRENT:
            motor.controller->SetCurrentSetPoint(0);
            break;
        case Motor::MODE_COMMAND_VELOCITY:
        case Motor::MODE_PWM_VELOCITY:
            motor.controller->SetVelocitySetPoint(0);
            break;
        case Motor::MODE_COMMAND_POSITION:
        case Motor::MODE_PWM_POSITION:
            motor.controller->SetPositionSetPoint(0);
            break;
        case Motor::MODE_COMMAND_Trajectory:
        case Motor::MODE_STEP_DIR:
        case Motor::MODE_STOP:
            break;
        }
        break;
    case ButtonBase::CLICK:
        // printf("KEY2\r\n");
        motor.controller->ClearStallFlag();
        break;
    }
}

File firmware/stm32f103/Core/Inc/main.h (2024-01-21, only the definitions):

#define ID0_Pin GPIO_PIN_8
#define ID0_GPIO_Port GPIOA
#define ID1_Pin GPIO_PIN_9
#define ID1_GPIO_Port GPIOA
#define ID2_Pin GPIO_PIN_10
#define ID2_GPIO_Port GPIOA
#define LED1_Pin GPIO_PIN_13
#define LED1_GPIO_Port GPIOB
#define LED2_Pin GPIO_PIN_14
#define LED2_GPIO_Port GPIOB
#define POWER_U_Pin GPIO_PIN_0
#define POWER_U_GPIO_Port GPIOA
#define DRV_TEMP_Pin GPIO_PIN_1
#define DRV_TEMP_GPIO_Port GPIOA
#define HW_ELEC_BM_Pin GPIO_PIN_2
#define HW_ELEC_BM_GPIO_Port GPIOA
#define HW_ELEC_BP_Pin GPIO_PIN_3
#define HW_ELEC_BP_GPIO_Port GPIOA
#define HW_ELEC_AM_Pin GPIO_PIN_4
#define HW_ELEC_AM_GPIO_Port GPIOA
#define HW_ELEC_AP_Pin GPIO_PIN_5
#define HW_ELEC_AP_GPIO_Port GPIOA
#define BUTTON2_Pin GPIO_PIN_13
#define BUTTON2_GPIO_Port GPIOC
#define HW_ELEC_APWM_Pin GPIO_PIN_10
#define HW_ELEC_APWM_GPIO_Port GPIOB
#define HW_ELEC_BPWM_Pin GPIO_PIN_11
#define HW_ELEC_BPWM_GPIO_Port GPIOB
#define BUTTON1_Pin GPIO_PIN_12
#define BUTTON1_GPIO_Port GPIOB
#define SPI1_CS_Pin GPIO_PIN_15
#define SPI1_CS_GPIO_Port GPIOA
#define RS486_RE_Pin GPIO_PIN_11
#define RS486_RE_GPIO_Port GPIOA
#define REDUCE_RESOLUTION 1

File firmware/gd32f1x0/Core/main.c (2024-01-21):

#include "main.h"
#include "systick.h"
#include "common_inc.h"
#include "usart.h"
#include "spi.h"
#include "tim.h"
#include "adc.h"
#include "gpio.h"

/*!
    \brief main function
*/
int main(void) {
    
    /* configure systick timer for delay_ms() function */
    systick_config();
    /* 4 bits for preemption priority 0 bits for subpriority */
    nvic_priority_group_set(NVIC_PRIGROUP_PRE4_SUB0);

    /* configure peripherals */
    gpio_config();
    adc_config();
    uart_config();
    timer1_config();
    timer13_config();
    pwm_timer2_config();
    spi_config();

    Main();

    while (1) {
        
    }
}

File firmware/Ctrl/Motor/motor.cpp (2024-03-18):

#include "configurations.h"
#include "motor.h"

#include <cmath>

#define REVERSE_DIR(NUM) (boardConfig.reverse_direction ? -(NUM) : (NUM))

void Motor::Tick20kHz()
{
    // 1.Encoder data Update
    encoder->UpdateAngle();

    // 2.Motor Control Update
    CloseLoopControlTick();
}


void Motor::AttachEncoder(EncoderBase* _encoder)
{
    encoder = _encoder;
}


void Motor::AttachDriver(DriverBase* _driver)
{
    driver = _driver;
}


void Motor::CloseLoopControlTick()
{
    /************************************ First Called ************************************/
    static bool isFirstCalled = true;
    if (isFirstCalled)
    {
        int32_t angle;
        int32_t HomeOffset = config.motionParams.encoderHomeOffset % MOTOR_ONE_CIRCLE_SUBDIVIDE_STEPS;
        if (HomeOffset < MOTOR_ONE_CIRCLE_SUBDIVIDE_STEPS / 2)
        {
            angle =
                encoder->angleData.rectifiedAngle >
                HomeOffset + MOTOR_ONE_CIRCLE_SUBDIVIDE_STEPS / 2 ?
                encoder->angleData.rectifiedAngle - MOTOR_ONE_CIRCLE_SUBDIVIDE_STEPS :
                encoder->angleData.rectifiedAngle;
        } else
        {
            angle =
                encoder->angleData.rectifiedAngle <
                HomeOffset - MOTOR_ONE_CIRCLE_SUBDIVIDE_STEPS / 2 ?
                encoder->angleData.rectifiedAngle + MOTOR_ONE_CIRCLE_SUBDIVIDE_STEPS :
                encoder->angleData.rectifiedAngle;
        }

        controller->realLapPosition = angle;
        controller->realLapPositionLast = angle;
        controller->realPosition = angle;
        controller->realPositionLast = angle;

        isFirstCalled = false;
        return;
    }

    /********************************* Update Data *********************************/
    int32_t deltaLapPosition;

    // Read Encoder data
    controller->realLapPositionLast = controller->realLapPosition;
    controller->realLapPosition = encoder->angleData.rectifiedAngle;

    // Lap-Position calculate
    deltaLapPosition = controller->realLapPosition - controller->realLapPositionLast;
    if (deltaLapPosition > MOTOR_ONE_CIRCLE_SUBDIVIDE_STEPS >> 1)
        deltaLapPosition -= MOTOR_ONE_CIRCLE_SUBDIVIDE_STEPS;
    else if (deltaLapPosition < -MOTOR_ONE_CIRCLE_SUBDIVIDE_STEPS >> 1)
        deltaLapPosition += MOTOR_ONE_CIRCLE_SUBDIVIDE_STEPS;

    // Naive-Position calculate
    controller->realPositionLast = controller->realPosition;
    controller->realPosition += deltaLapPosition;

    /********************************* Estimate Data *********************************/
    // Estimate Velocity
    controller->estVelocityIntegral += (
        (controller->realPosition - controller->realPositionLast) * motionPlanner.CONTROL_FREQUENCY
        + ((controller->estVelocity << 5) - controller->estVelocity)
    );
    controller->estVelocity = controller->estVelocityIntegral >> 5;
    controller->estVelocityIntegral -= (controller->estVelocity << 5);

    // Estimate Position
    controller->estLeadPosition = Controller::CompensateAdvancedAngle(controller->estVelocity);
    controller->estPosition = controller->realPosition + controller->estLeadPosition;

    // Estimate Error
    controller->estError = controller->softPosition - controller->estPosition;

    /************************************ Ctrl Loop ************************************/
    if (controller->isStalled ||
        controller->softDisable ||
        !encoder->IsCalibrated())
    {
        controller->ClearIntegral();    // clear integrals
        controller->focPosition = 0;    // clear outputs
        controller->focCurrent = 0;
        driver->Sleep();
    } else if (controller->softBrake)
    {
        controller->ClearIntegral();
        controller->focPosition = 0;
        controller->focCurrent = 0;
        driver->Brake();
    } else
    {
        switch (controller->modeRunning)
        {
            case MODE_STEP_DIR:
                controller->CalcDceToOutput(controller->softPosition, controller->softVelocity);
                break;
            case MODE_STOP:
                driver->Sleep();
                break;
            case MODE_COMMAND_Trajectory:
                controller->CalcDceToOutput(controller->softPosition, controller->softVelocity);
                break;
            case MODE_COMMAND_CURRENT:
                controller->CalcCurrentToOutput(controller->softCurrent);
                break;
            case MODE_COMMAND_VELOCITY:
                controller->CalcPidToOutput(controller->softVelocity);
                break;
            case MODE_COMMAND_POSITION:
                controller->CalcDceToOutput(controller->softPosition, controller->softVelocity);
                break;
            case MODE_PWM_CURRENT:
                controller->CalcCurrentToOutput(controller->softCurrent);
                break;
            case MODE_PWM_VELOCITY:
                controller->CalcPidToOutput(controller->softVelocity);
                break;
            case MODE_PWM_POSITION:
                controller->CalcDceToOutput(controller->softPosition, controller->softVelocity);
                break;
            default:
                break;
        }
    }

    /******************************* Mode Change Handle *******************************/
    if (controller->modeRunning != controller->requestMode)
    {
        controller->modeRunning = controller->requestMode;
        controller->softNewCurve = true;
    }

    /******************************* Update Hard-Goal *******************************/
    if (controller->goalVelocity > config.motionParams.ratedVelocity)
        controller->goalVelocity = config.motionParams.ratedVelocity;
    else if (controller->goalVelocity < -config.motionParams.ratedVelocity)
        controller->goalVelocity = -config.motionParams.ratedVelocity;
    if (controller->goalCurrent > config.motionParams.ratedCurrent)
        controller->goalCurrent = config.motionParams.ratedCurrent;
    else if (controller->goalCurrent < -config.motionParams.ratedCurrent)
        controller->goalCurrent = -config.motionParams.ratedCurrent;

    /******************************** Motion Plan *********************************/
    if ((controller->softDisable && !controller->goalDisable) ||
        (controller->softBrake && !controller->goalBrake))
    {
        controller->softNewCurve = true;
    }

    if (controller->softNewCurve)
    {
        controller->softNewCurve = false;
        controller->ClearIntegral();
        controller->ClearStallFlag();
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

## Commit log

2024-01-01 add firmware
    [configurations.h, stlink.cfg]
2024-01-02 add motor-20 pcb
    [BOM-stepper-motor-20.csv, Power.kicad_sch, Power.sch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]
2024-01-21 add gd32f130 target
    [stlink.cfg]
2024-01-21 add reduce sensor resolution
2024-01-21 add modbus
    [configurations.h, 寄存器表.xlsx]
2024-01-21 update reg
    [寄存器表.xlsx]
2024-01-21 stm32: reduce time of spi transmition
2024-03-04 add reverse direction
    [configurations.h, 寄存器表.xlsx]
2024-03-18 add temperature and voltage threshold
    [Modbus_Register.xlsx, configurations.h, 寄存器表.xlsx]

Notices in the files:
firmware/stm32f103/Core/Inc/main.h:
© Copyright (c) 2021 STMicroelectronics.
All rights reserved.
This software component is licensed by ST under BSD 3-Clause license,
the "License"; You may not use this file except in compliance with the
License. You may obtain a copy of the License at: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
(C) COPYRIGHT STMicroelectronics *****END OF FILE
